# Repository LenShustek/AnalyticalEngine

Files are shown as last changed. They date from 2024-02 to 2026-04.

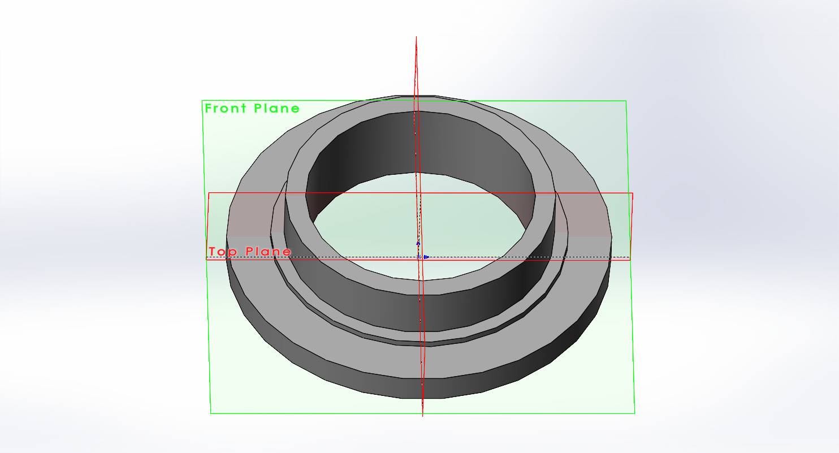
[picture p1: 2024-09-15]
Piers_Plummer_DE/parts/Fig_cyl_end.JPG

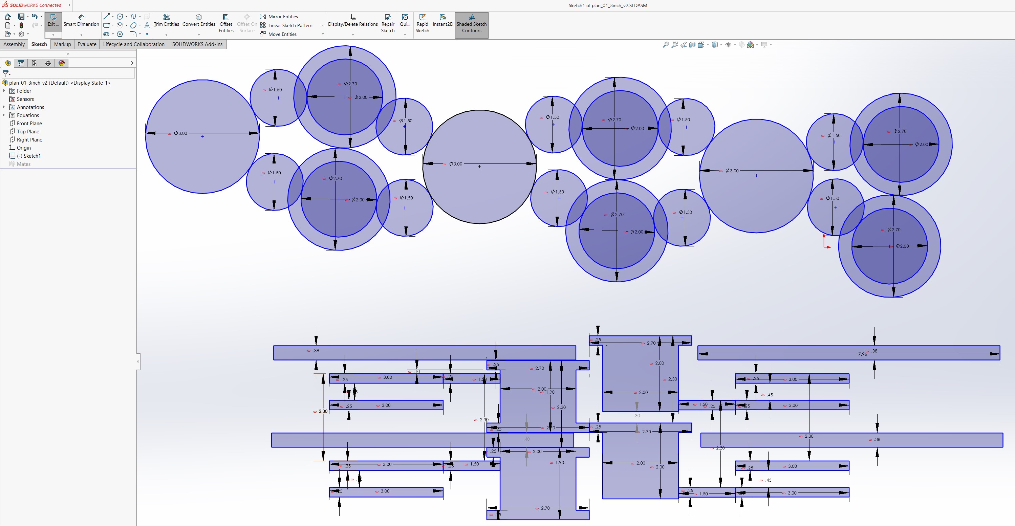
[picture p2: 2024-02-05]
test_designs/mill/plan_01_3inch_v2.jpg

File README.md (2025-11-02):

# Building the World's First Computer

This is a project to build the "first computer": a version of
Charles Babbage's entirely mechanical Analytical Engine. The original proposal is the file <ins>proposal_V0.5.pdf</ins> in this directory.

It is a major undertaking that will take years. As of the start of 2024 the effort has just begun.

This repository will reflect a work continually in progress. It will contain plans, 
notes, simulations, and designs as they are developed. Nothing here is static, and 
no decision is immutable until we start construction, and maybe not even then. 

I posted a 30-minute talk about the project here: https://youtu.be/HRmGAhwOo0s

19 April 2024: As changes are made to reflect progress, this repository is starting to look more like a blog, especially recently in the test_designs/anticipating_carriage section. GitHub is not the right vehicle for that, so I've transitioned instead to using a real blog: https://worldsfirstcomputer.blogspot.com/. I'll keep putting design and code files here, but the narrative (in the conventional reverse chronological order) will now be in the blog.

If you are interested in this project, the place to start is the latest version of the proposal
document in this directory. It will be modified occasionally, but there is a log at
the end that highlights what has changed.

Other directories will appear as various parts of the project are developed. 
These are the first to be added:
- simulations
  - instruction_simulator
  - timing_simulator
  - component_simulator
- test_designs
  - digit_wheel
  - anticipating_carriage
  - mill
     
Wish us luck. 

Len Shustek
4 February 2024

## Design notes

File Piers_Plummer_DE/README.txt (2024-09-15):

An absolutely extraordinary partial model of Charles Babbage's Difference Engine #2 was built in 2017 by Piers Plummer at Royal Holloway, University of London. You can see it in action here:
https://www.youtube.com/watch?v=IhnA-oAwh04
Amazing!

It is a simplified version of the DE with 4 columns of 6 digits each, opened out more than the original design for better visibility. It is made of 3D-printed and painted nylon, laser-cut steel, and other standard modern parts. "And of course, it had to be powered by steam!"

In order to learn from their detailed design, and to see that it gets the public exposure and preservation that it deserves, I asked for and received permission to make the CAD files available in this GitHub repository.

The design files were made with Solidworks. For those of without access to that CAD software, I created and included JPG images of each of the parts and assemblies.

This was a project with the Centre for Software Language Engineering at the Computer Science Department of Royal Holloway, University of London, funded by The Leverhulme Foundation with support from the Engineering and Physical Sciences Research Council. The participants in the project were:
   Dr. Doron Swade
   Prof Adrian Johnstone
   Prof Elizabeth Scott
   Dr. Piers Plummer
http://babbage.csle.cs.rhul.ac.uk

Well done!

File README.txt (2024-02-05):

This is a project to build the "first computer": a fully mechanical version of
Charles Babbage's Analytical Engine. It is a major undertaking that will take years.
As of the start of 2024 the effort has just begun.

This repository will reflect a work continually in progress. It will contain plans, 
notes, simulations, and designs as they are developed. Nothing here is static, and 
no decision is immutable until we start construction, and maybe not even then. 

If you are interested, the place to start is the latest version of the proposal
document in this directory. It will be modified frequently, but there is a log at
the end that highlights changes.

Other directories will appear as various parts of the project are developed. 
These are the first to be added:
  simulations
     instruction_simulator
     timing_simulator
     component_simulator
  test_designs
     digit_wheel
     anticipating_carriage
     mill
     
Wish us luck. 

Len Shustek
4 February 2024

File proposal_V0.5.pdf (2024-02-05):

# Building the World’s First Computer

# Charles Babbage’s “Analytical Engine”

## Len Shustek

4 February 2024, version 0.5

# Introduction

Charles Babbage, as historian Doron Swade likes to say, is equally famous for two things: inventing the digital computer, and failing to build it.

Babbage began his first design for a computer, which he called the Analytical Engine, in 1834, at the age of 43. He worked on that and subsequent designs for most of the next 37 years, until his death in 1871. During that time he created “Plans” for at about 35 different Engines, each with varying degrees of details worked out. Unfortunately none of the Plans was a complete design with a set of drawings from which parts could be built and a computer assembled.

We are left with a rich collection of ideas, drawings, notes, mechanical designs, timing diagrams, and descriptive symbolic “Notations” for an entire family of unfinished computers that no attempt was ever made to build.

The challenge we wish to pose is: Can we, 185 years later, build a fully functional mechanical computer of the kind that Babbage envisioned?

# Contents

# Executive summary

The dawn of the computer age is generally situated in the middle of the 20th century, at about the time of World War II. Although we crave heroic individual inventors for important technological advances – like Bell for the telephone, and Edison for the lightbulb – the situation for the computer is much more complicated.

If, however, we travel back to the middle of the 19th century, we discover a lone genius named Charles Babbage who devoted his life to inventing calculating machines. The most innovative of those machines was a programmable digital computer that he called an Analytical Engine.

The problem with anointing him on that basis as the sole inventor of the computer is that he never built it. We don’t know if his ideas were sound, or if his computer would have worked.

The project we wish to undertake is to build a working version of Babbage’s Analytical Engine, or at least something close enough to it that will demonstrate to the world that he fully deserves to be considered the inventor of the computer.

The Engine we propose to build is an entirely mechanical monstrosity, perhaps 12 feet long, 6 feet wide, and 10 feet high, made of gears, wheels, levers, and cams. It is programmed with “software” that is encoded by punched holes in rigid cards that are sewn together into continuous chains. It is animated by a single rotating shaft, which we would ideally like, in the spirit of Victorian technology, to be powered a steam engine. Useful computations will take 10 to 30 minutes, and the results will be observable afterwards as 30-digit decimal numbers shown on 7-foot tall columns of digit wheels.

This project is likely to take 3 to 5 years and cost 2 to 4 million dollars. The final year is the assembly and debugging phase, which we propose be staged in public view as a “living”
museum exhibit.

Assuming we achieve success and have a reliable operating Analytical Engine, it would then become a permanent, regularly demonstrated, and no doubt wildly popular exhibit.

This is an ambitious project, but the obligation to create a just record of history motivates us to undertake it.

Posterity, and Charles Babbage, deserve it.

# Part 1: the project and its background

# Related Babbage machines

In addition to designing computers, Babbage also designed mechanical calculators he called “Difference Engines”. These were special-purpose non-programmable machines that compute and tabulate values of polynomial equations that can be used to approximate a wide variety of mathematical functions. Like all traditional calculators, they are fundamentally different from computers in that they don’t follow instructions we call “software”. The Analytical Engine, in contrast, would have been of an entirely new and different class.

From 1823 to 1842 Babbage made an attempt to build his first Difference Engine using funding provided by the only venture capitalist of the day: His Majesty’s government. The project ended as a complete failure for a variety of reasons, including that Babbage had become more interested in his new idea for a computer.

Between 1846 and 1849 Babbage took time off from working on the computer to design an improved calculator, Difference Engine #2. He completed the design in full and meticulous detail, but he made no attempt to build it.

Some 140 years later, from 1985 to 1991, Doron Swade at the Science Museum in London led a bold project to build Difference Engine #2 exactly according to Babbage’s plans, with fabricated parts that have mechanical tolerances no better than what Babbage’s machinists could have achieved. It was a spectacular success. The machine works perfectly, demonstrating both that the design was correct and that Babbage could have built it. We can only conclude that the reasons for his failure were managerial and organizational, not technical.

Is the same true of his computer, the Analytical Engine? With the right management and funding, might we have had a computer a century earlier than we actually did?

The Science Museum ultimately built two copies of Difference Engine #2 as well as the integrated printer that was also designed by Babbage. The first copy stayed there and is run by curators only occasionally. The second one was loaned by its private owner to the Computer History Museum in California, where it was demonstrated by volunteer docents daily for 8 years, to the amazement of hundreds of thousands of visitors. In 2016 it was moved to the owner’s personal site and is now also rarely operated.

# On the prospects for building a complete Babbage Analytical Engine

There is a long-term vision for a project that would choose one of Babbage’s 35 plans for Analytical Engines, complete the many parts of that design that he had left undone, and build it as an historically accurate incarnation of one of his imagined computers.

This may someday be possible. But building an engine that adheres strictly to any of Babbage’s Plans is a massive undertaking and will be very difficult. Here are some of the issues:

- Only the later engines, starting with Plan 27, have conditional branches and loops that qualify them as modern-style general-purpose computers. Earlier designs do not, and so are less interesting as precursors of what was reinvented in the 20th century.
- Babbage prized both generality and high performance, with the result that all of those later Plans are frighteningly complex.
- The design for the chosen Plan would have to be completed in a way we might imagine him doing. There are substantial subsystems (like the interaction between user-level instructions and the microcode, and the transmission of barrel¹
stud movements to the
rest of the machine) as well as many important smaller mechanisms that are not designed. It is not just a few minor details that are missing.
- The complex mechanisms he did design have never been built or simulated, and some of them (like the selection mechanism for table-driven division) are devilishly hard to understand. We would have to convince ourselves, by reasoning or by simulation, that they would work correctly.
- For historical authenticity there might be pressure to use only materials and perhaps even methods that would have been available to Babbage, which increases the difficulty. It will be a challenge. In 2012 Doron Swade said of the magnitude of such a project²
, “I
reckon on 15 to 20 years to construct, and between 20 and 40 million dollars”.

1 The “barrels” are rotating cylinders with vertical columns of preset studs that control operations in the machine during a cycle, which is either 15 or 20 basic time units. The barrel rotates to a new position for each cycle by an amount that may depend on the data being manipulated. Depending on the Plan, Babbage proposed from one to five barrels, each of which can be viewed in modern terms as an independently executing microprogram.

2
“Mission Impossible: Constructing Charles Babbage’s Analytical Engine”, Dartmouth University, 8 May 2012, https://www.youtube.com/watch?v=FFUuN-ZRLz8

# The proposed project

As an alternative -- or perhaps as a prelude -- to choosing, completing, and constructing an historically accurate instantiation of one of the full Babbage engines in the course of a 15 to 20 year project, I propose that we build a “Babbage-inspired” smaller Analytical Engine. It will still be a fully-functional mechanical digital computer run by software, but it will be much simpler because it implements only a subset of the many features that are in Babbage’s highly developed Plans.

In 1840 Babbage briefly considered such a machine, designated as Plan 26, but he was discouraged by the poor theoretical performance and did not pursue it. Again at the end of his life he considered -- and actually started constructing -- a different simplified engine that he called “the Model”, which might be considered his final Plan 35. The incomplete fragment he built is at the Science Museum in London, but no drawings of what he intended for the complete machine survive.

The functionality of our proposed small engine is in line with both of those. Our goals are threefold:

- to gain experience with constructing a mechanical computer using Babbage-designed mechanisms that might inform later attempts to build one of the complete Babbage engines
- to help justify the assertion that Babbage is the inventor of the computer
- to create an engaging public museum exhibition of a programmable computer that could have been built a century before it was actually first achieved

We are not overly concerned with performance, because we can choose specific demonstration problems that execute in a reasonable time given the characteristics and generality of the smaller engine. We wish instead to emphasize the novel and prescient aspects of his instruction sequencing and microprogram control, which predated the reinvention of electronic equivalents by over a hundred years.

Will this be an “authentic” Babbage Analytical Engine? No, and yes.

No, in that we are not implementing a specific Babbage design, and we are not using only materials that he would have used. It will not look in its details exactly like an engine he could have built, and it will not have some internal features that were in many of his designs.

Yes, in the sense that it is it is an honest amalgam from several of his designs. It will use only architectures and mechanisms he designed, and it will functionally be a faithful subset of many of his unbuilt computers. It fully inherits the spirit of his ambitions.

We will be careful to describe this not as “The Babbage Analytical Engine” (as if there were one), but as a “Babbage-inspired”, “Babbage-like”, or “Babbage subset” computer. See Appendix 1: proposed exhibit placard.

# Related projects

There is a complementary formal organization already in place. Plan28 (www.plan28.org) was established in December 2011 as UK non-profit charity #1145043 whose stated mission is “to build a Babbage Analytical Engine for historical and educational purposes.” It has four volunteer trustees (Doron Swade, John Graham-Cumming, Tim Robinson, Johnathan Rosser Histed) and no employees. The reported total gross income has been less than £1K per year since inception. Its 2013 appeal to accumulate financial pledges on www.justgiving.com has been suspended. As of March 2023 several attempts to solicit additional participation in the activities of Plan28 had not been successful

After 12 years, the major accomplishment of Plan28 has been the incredible six years of work that Tim Robinson (a docent at the Computer History Museum in California) has done as a volunteer, cataloging and analyzing the 7000 pages of documents that Babbage left behind relating to the Analytical Engine. Tim is writing what will be the definitive scholarly exposition on the evolution of plans for the Analytical Engine during Babbage’s lifetime.

Tim’s work is monumental, and provides important background for understanding Babbage’s designs. But it does not contain within it a proposal for a modern construction project. No resources have been applied to that.

The Plan28 project is committed to choosing, completing, and faithfully building one of Babbage’s full designs, and doing it in the UK. Our goal is to build a reduced design, and to do it in the US. The projects are compatible and harmonious, but different and independent.

# Project phasing, timeline, cost, venue, and funding

Doron Swade’s estimate of 15-20 years and $20-40M for the full engine build was based, as he says, “on the classic and traditional engineering fudge factors, guess work, divination, [and] astrological prediction”.

At this point we can do no better than that for the proposed smaller engine. We have only uninformed wild guesses, of which this is the first one:

phase | for what | time | money
1 | architectural design, including register-level simulation | 6 months | $0
2 | detailed mechanism design, including some mechanical connectivity simulation and prototype construction; develop test and evaluation plans | 1 year | $0
3 | CAD part drawings, including limited motion simulation of some subsets | 1 year | $250K
4 | part fabrication and procurement | 6 months | $1M
5 | assembly and debugging | 1 year | $250K
| totals | 4 years | $1.5M

The cost for parts was guesstimated thusly: The most numerous part is the digit wheel. We have a quote of less than $2 each for 3D-printing them in China out of nylon. We need about 1700, so $3400. Quadruple that cost to account for metal shafts and surrounding supports, so $14K. Assume we need 4 times as many parts for the rest of the engine (so 6800, of which some are custom and some are stock) that cost $150 each on average, and the total comes to $1.03M³
This is, of course, a gross and premature estimate.

The two chunks of $250K are for professional salaries. The rest of the labor, including management, comes from volunteers. We might be able to get some contributed professional labor from related companies, like Autodesk.

Clearly these completely fabricated estimates cry out to be quickly and periodically refined as the design becomes more specific.

3 Note that the most numerous part – the figure wheels – are an insignificant part of the total!

The first four phases require no venue, other than modest storage for parts as they arrive during phase 4. Assembly would most preferably happen as a year-long public exhibit at the Computer History Museum in California, at no cost for the space. The machine would then, if successful, become a permanent museum exhibit and be operated daily by trained volunteer docents.

I expect that raising $1M to $2M ($2M to $4M if we are off by a factor of 2) for this project from a small number of interested individual donors will not be difficult. Corporate sponsorships are also possible and would be welcome.

This is a difficult but definitely achievable undertaking that will be a major contribution to the history of computing and therefore of our modern age.

# Part 2: technical details

We here codify two sets of propositions for the construction of the small engine:

1. guiding principles for making design decisions, including those that will allow the engine to qualify as “Babbage-inspired”, or “an amalgam of Babbage’s designs”
2. the design decisions, based on those principles, that determine the detailed characteristics of the Engine we will build
These are strawman proposals. After they have been debated, modified, and accepted, we can move on to the next phases of the project: detailed design, simulation at several levels, part drawings and specifications, prototype testing, fabrication, and assembly.

# The principles

1. The top-level goal is to exhibit the practicality of a general-purpose programmable mechanical digital computer that could have been built using Babbage-designed mechanisms in the 19th century. It is not, as was motivating Babbage, to build a machine that will actually be used for utilitarian table-making, or for novel mathematical research.
2. We are not picking one of Babbage’s extremely complex Plans to implement. None of them were complete, and some of the Plans closest to being complete violate other of these principles.
3. We are instead building an Engine that is “inspired by” Babbage’s designs. We will pick from among his algorithms and mechanisms, from whichever of his Plans they were in, to create an achievable modern Plan that has a high likelihood of success.
4. We will include all the features necessary to demonstrate that the engine is a fully general programmable computer in the spirit of those we build today. That includes the ability to create program loops, and to execute conditional transfers that are based on computed results.
5. Maximum performance is not an objective, as it was for most of Babbage’s Plans. Our objective is “reasonable” performance that is suitable for demonstrations.
6. We place high value on simplification, subject to the “reasonable” performance objective.
7. We place high value on avoiding the use of untested or novel mechanisms that might increase the risk of failure.

8. We place high value on having only one kind of each distinct part type, not multiple variants. So, if we can: only one kind of Figure Wheel, only one kind of barrel pickoff lever, etc.
9. All things being equal, we would prefer to make more copies of a smaller number of parts that we can develop high confidence in, rather than to use unique, unproven, or complex mechanisms.
10. We will primarily use architecture and mechanisms that had been proposed by Babbage for some Plan, or variations of them that we could easily imagine him devising given the appropriate motivation. We are rarely if ever allowed to invent new mechanisms, and only if the need is compelling, and only if they are in the style of those he devised.
11. We will not be constrained to use only engineering processes that were available to Babbage. We unapologetically use modern tools for simulation, design, and manufacturing.
12. We will not be constrained to use only materials that were available to Babbage. Plastic parts fabricated using 3D printing, for example, are fair game.
13. We wish the resulting Engine to be demonstrated regularly in a museum environment, so we will need to choose and achieve appropriate quantitative targets for performance, life expectancy and reliability.
14. Our focus is on building the calculating engine. We will leave the building of printing⁴ and/or plotting apparatuses, both of which interested Babbage, to future generations.

4 Note that the printer designed by Babbage for Difference Engine #2 and built by the Science Museum London in the 1990s would work equally well, with minor changes in the interface, for the Analytical Engine.

# The design decisions and the rationales therefor

1. Numbers have 30 digits.
- Babbage’s designs varied from 25 to 60 digits per number, stored as a set of rotating “digit wheels” that are stacked vertically on a common axis with the units position at the bottom. That may at first seem like an excessive number of digits, but because there was no floating point number representation, long numbers are required to support a large dynamic range.
- 30 digits is more than adequate for demonstration purposes. We could even do with fewer.
- Increasing the number of digits in numbers has a surprisingly modest impact on the details of the design. But it does increase drive force requirements, change the framing system, increase the overall height, and increase cost. We would do that only if further analysis provides the justification.
- The Difference Engine #2 built in the 1990s had 31 digit numbers, so we would be in good company. We would feel comfortable about the complexity and utility anywhere in the 20-40 digit range.

## 2. Use sign-magnitude representation for numbers in the

store.

- Babbage proposed this representation in all mature versions of the Engine.
- The sign is stored on an additional (31st) Figure Wheel, with any even number representing positive, and any odd number representing negative.
- This is convenient for user interaction, and for multiplication and division.
- It does complicate addition and subtraction, which will sometimes require extra cycles to convert to 9’s complement form suitable input for the adder, and to convert negative numbers back to sign-magnitude for storage.

## 3. Use 9-cycle whole-zero operations for Giving Off⁵ transfers

- Starting with Plan 28, Babbage proposed a clever “half-zero” idea which almost doubles the speed of transfers by turning wheels in either direction during Giving

5
“Giving Off” is the process of rotating all the digit wheels of a number axis so that they become zero, while at the same time adding the original values to the digit wheels of another axis. When using “whole-zero“ it takes one cycle of 15 time units: 1 time unit for receiving the directive from the microprogram barrel, 2 for putting the axes into gear, 9 for the rotation, and three for engaging the locks that prevent any further movement of the wheels.

Off. But it almost doubles the number of wheels, and it adds complexity to the Anticipating Carriage. We do not embrace that tradeoff.

## 4. Do addition using an anticipating carriage

- Babbage was justifiably proud of his clever design that performs all the carries for a multi-digit addition in parallel, in a small amount of time that is independent of the number of digits in the values being added.
- We accept the complexity of this mechanism both to improve performance for a common operation and to honor the genius of its inventor.
- We do not implement his “hoarding carriage” for consecutive additions that accumulates up to 10 carries for later inclusion into the sum.

## 5. Multiplication and division are implemented without using a table of multiples of the multiplicand or divisor

- Most of Babbage’s mature Plans precomputed nine multiples of the multiplicand or the divisor, in the interest of increased speed during the computation of the product or quotient.
- That scheme requires nine additional “Table Axes” to be built, and several cycles of additional overhead time at the start of a multiplication or division. It represents a significant increase in parts and complexity.
- In many cases it also results in a significant performance improvement. But it actually reduces performance for some simple cases where the overhead of constructing the tables dominates.
- To support our decision not to use tables, I did timing simulations using random operands of various lengths. See Appendix 2: multiplication and division timing charts for graphs that elucidate and quantify the cases where the tables help. The conclusion is that we can minimize the performance hit of not using tables if we avoid long multipliers and long dividends with small divisors.
- We will select demonstration programs so that the lack of precomputed tables is not a serious issue. Babbage, in his quest for general applicability of the engine to a wide range of problems, did not have that option.
- That said, it is historically important that we be able run the program to compute Bernoulli Numbers whose trace Ada Lovelace documented in Note G of her 1843 translation of Luigi Menabrea’s paper on the Analytic Engine, and in that case we will suffer from not using the tables. See Appendix 3: calculating Bernoulli numbers.

- Babbage eliminated the tables twice: once for the short-lived Plan 26 in 1840, and again for what Tim Robinson calls Plan 35 in 1869-1870. Babbage called that his “model”, and used the design to actually start construction, for the first time, of an Analytical Engine. It was still incomplete at the time of his death in 1871, but the fragment is preserved in the collection of the Science Museum in London:
https://collection.sciencemuseumgroup.org.uk/objects/co62245/babbages-analytical-engine-1834-1871-trial-model-analytical-engine-mill (https://collection.sciencemuseumgroup.org.uk/objects/co62245/babbages-analytical-engine-1834-1871-trial-model-analytical-engine-mill)

## 6. Multiplication will generate only a single-precision 30 digit result

- Many of Babbage’s Plans generate a double-precision result from multiplication that is stored on two axes, so that (1) all product digits are always retained, (2) overflow cannot happen, and (3) the result can be used as a double-precision dividend for division by a single-precision divisor.
- But doing so requires complexity which we think is not worthwhile for our smaller engine.
- We will instead detect overflow during single-precision multiplication and signal it to the operator, which is a scheme that Babbage proposed to use in several other cases.
- This is not an uncommon limitation for later computers. Having a single-precision multiplication result matches the model of integer arithmetic implemented a century later by most programming languages. When you multiply two integers in Fortran or C, you don't get a double-precision result that can then be used as the double-precision dividend for a division. It is true that in that environment there is the option of switching to floating point for greater range. But their integers don't hold the equivalent of 30 decimal digits, so the need for floating point is more pressing. And anyway the early floating point formats, like for the IBM 704, had a maximum single-precision exponent of only 2

128 (10³⁸)so they
were not that much better than 30-digit integers. We would be quite happy if our Analytical Engine had computational capability similar to the IBM 704 from 1954.

## 7. Implied decimal points are implemented

- In some Plans Babbage allowed the user to specify an implied decimal point that was “d” digits to the left of the least significant digit.
- The source of “d” isn’t always clear. In Plan 13 it is assumed to have been set manually by the operator on a special figure wheel of a particular Mill axis.

- Implementing this requires additional barrel microcode complexity, and additional time for division to generate more quotient digits. For multiplication, the required right shift of the product might overlap with other operations and take no extra time. There is no impact on addition and subtraction.
- We initially decided against implementing this. But the desire to execute, unmodified, the famous 1843 Lovelace program to compute Bernoulli Number B7 caused a reversal of the decision.
- The alternative is to require the programmer to scale up operands appropriately, and to use the explicit shift (“step up” and “step down”) instructions when necessary.

## 8. Square root is not implemented

- This was a feature in early Plans, but by Plan 16 even Babbage had discarded it, complaining that “It doesn’t do cube roots.”

## 9. Approximate multiplication and division is not implemented

- In some Plans Babbage proposed versions of multiplication and division that were faster because they operated on fewer digits. He thought they would be useful for certain mathematical approximation methods, which typically do not require full precision in the early stages.
- If this requires more than a trivial modification to the full-precision algorithms, it is not worth the additional complexity. But if it is simple, and if it speeds up no-table multiplication and division, it may be worth doing.

## 10. We do support pipelined streamed addition/subtraction

- In some Plans Babbage allowed for a succession of variables coming from the store to be added to an accumulating value in the mill. All, some, or only the final value of the sum is written back to the store, as directed by the cards.
- Babbage didn’t, unfortunately, provide modern-style registers -- or even a single accumulator – to retain data in the mill between operations. Hence computing the sum of a sequence of values without streamed additions is painfully slow, since each intermediate value has to be written back to the store and then reread. A simple addition or subtraction of numbers in the store takes 6 cycles of 20 time units each, or about 19 seconds. Adding ten numbers would take 190 seconds.

- With pipelined streaming, adding ten variables takes about 44 seconds instead, a 4.3x improvement. That is a significant enough savings for a common operation to warrant the extra complexity.
- This is also a stellar demonstration of “microcode” in Babbage’s design that is distributed among independently operating barrels.

## 11. The store

- The store will contain 25 axes. Each axis has 31 cages

6
, and each cage holds two
digits, for a total storage of 50 signed 30-digit numbers in sign-magnitude format.
- ENIAC, which after its 1947 conversion was the first stored-program electronic computer to solve serious research problems⁷
, had only 20
10-digit numbers. We will have over twice that in both metrics.
- The store is arranged linearly, with transfers to the Mill effected via straight geared racks.
- Readout from the Store is not destructive, because returning the racks to their home position after “giving off” and transferring the value to the Mill will restore it to the Store axis. (There is a suspected timing problem in Babbage’s design for this that will need to be resolved.)

## 12. On the engagement of axes

- We will investigate having axes engage with racks and with other axes by being raised or lowered, which also selects one of the two numbers. There is then no need for additional axes with pinion gears.
- This was proposed by Babbage in Plan 28, although we are not also adopting that Plan’s half-zero scheme for giving off.
- The feasibility of doing this will depend on the geometry of the machine layout in the various areas. In the Mill, additional columns with small pinion gears may be necessary to engage figure wheel axes that can't be put close enough to another to allow lifting to effect engagement with their intended partner.
- Raising and lowering axes to effect engagement may also complicate the support structure that keeps digits wheels separated by a constant distance.

6 A “cage” contains two or more adjacent digit wheels from unrelated numbers at the same decimal position on an axis. See Digit wheel parameters.

7
See the description of Klara von Neumann’s Monte Carlo simulation program for hydrogen fusion as described in “ENIAC in Action” by Haigh, Priestley, and Rope, MIT Press 2018.

## 13. The user-level instruction set

As Tim Robinson says in his treatise, “This is perhaps the least well elaborated aspect of the mature Engine, and one in which he [Babbage] showed much indecision.”

We will need to define the format and encoding for Operation, Variable, and Number cards, which together form what is today called a program. Each type of card is fed as a separate connected loop to one of three card-reading prisms.

Focusing on the Operation cards, we propose the following for what we would today call the “machine language instruction set”:

1. algebraic addition
2. algebraic subtraction
3. algebraic multiplication, producing a 30-digit result
4. algebraic division, using a 30-digit dividend and divisor
5. ascertaining if a variable is zero
6. ascertaining if a variable has a positive or negative sign
7. reading a number card into storage
8. stepping up (multiplying by 10)
9. stepping down (dividing by 10)
10. turn cards forward (forward jump; see S/2/2.339 in the Babbage archive)
11. turn cards back (backward jump; see S/2/2.339)

Except for the change to single-precision for multiplication and division, these are all operations that were proposed by Babbage for Plan 27.

Pipelined streamed addition or subtraction doesn’t require an additional instruction type because it is encoded on the normal addition or subtraction operation card. We can choose one of the two possible schemes Babbage described:

1. The operation card (or a Store location) contains an index which indicates the number of operands to be operated on, each fetched using a new variable card. When all the operands have been processed, a second addition or subtraction operation card then orders the result to be written to the store. The semantics of addition and subtraction instructions are thus context sensitive.
2. A new operation card is read with each variable card, and it indicates when the accumulated result should be written to the store. In this case multiple partial results could be written.

The critical new features in Plan 27 were the tests (5 and 6), which make the Analytical Engine a universal Turing-complete computer. The design, however (quoting Tim Robinson), “is not very clear regarding the actions that will be taken depending on the result of the test.” It is most likely that small indices on the operation and variable cards indicate how many of those types of cards should be skipped, and whether in the forward or backward direction, if the condition being tested is satisfied.

## 14. Digit wheel parameters

The digit wheel is the basic storage unit for one decimal digit. Its geometry affects everything in the engine.

- considerations for the digit wheel size:
- In all of Babbage’s designs through Plan 25 the diameter of the digit wheels were 4”, although some isolated wheels on certain axes in the Mill were as large as 8”.
- In Plans 27 and 28 he changed to 3” wheels for the store and table axes.
- In plan 30 he reduced it further, to 1-1/4”.
- Smaller wheels are better because the mass (proportional to the square of the diameter) is reduced, and because it allows axes to be placed closer together, which in turn reduces the required size and mass of racks and the supporting framework.
- But smaller wheels are worse because they require more precision, and even small accidental motions can cause derangement.
- considerations for interleaving the digits of multiple numbers on one axis:
- All number columns in the Mill and the Store must have the same inter-digit spacing.
- The inter-digit height required by the anticipating carriage mechanism leaves room for 2 or more digit wheels from separate numbers to be stored at each of the 30 digit positions along an axis.
- Plans 1 to 13 used 3-5/8” high cages that hold digits from 4 different numbers.
- Plans 14 to 27, thanks to a more compact mechanism Babbage devised for the anticipating carriage, used 2-7/8” high cages holding digits from 2 different numbers.
- Plans 28 used 1-5/8” cages with 2 numbers.
- Plans 30 and beyond proposed using pressure die casting or metal stamping to achieve cage heights of 5/8” or even smaller.

- We propose to adopt the Plan 27 intermediate wheel size and its corresponding cage height, digit spacing, and digit speed. The complete set of wheel parameters is thus:
- DP (“diametral pitch”) of 10, which means 10 teeth per inch of diameter
- That sets the size of the teeth and the width of locking bars
- 3 inch diameter wheels, so 30 teeth/wheel
- 3 copies of 0..9 on each wheel, which means a 0.314 inch “unit of space” between digit positions, and one tooth per digit position
- 2 inch/second maximum surface speed, which means a 0.157 second “unit of time” for single digit position movements
- preliminary investigation indicates that the cage height could be as small as 2.3 inches
- 2 digits per cage
- a 30-digit column plus sign that holds two numbers is then about 6 feet high
- There is mechanical overhead, mostly underneath the digit columns, that will occupy an additional 3 or so feet.
- For maintenance it may be necessary to allow enough ceiling height to pull an axis out the machine vertically. That could require about 16 feet of ceiling clearance above the floor.
- The same digit wheel configuration is also used in the Store, which therefore holds twice as many numbers as it has axes.
- In the Mill, some of the axes may only need or require only 1 digit per cage.
- In general we will endeavor to use this as the only figure wheel format in the engine, consistent with principle #8.

## 15. Powering the engine

In the interest of making the museum experience as historically authentic as possible, it would be gratifying to be able to power the machine with a live steam engine.

The steam engine would need to be of the condensing kind -- not to improve efficiency, but so that steam is not vented indoors. The boiler would be modern, electric⁸
, and located outside the demonstration area.

8
Like, for example, https://catalog.electrosteam.com/item/process-steam-generators/lg-10-40-electric-steam-generators/lg-10-h (https://catalog.electrosteam.com/item/process-steam-generators/lg-10-40-electric-steam-generators/lg-10-h)

It is not clear if we can pull this off. Steam-operated equipment is generally subject to extensive safety, inspection, and even training/certification regulations. Since our boiler would be less than 400,000 BTU/hour it would be exempt from many of the regulations, but it would still likely require a waiver of normal building codes to secure a permit for installation.

Providing power in the 2-5 HP range should be easy, but at this point we don’t know what will be required.

Using compressed air to drive an air motor could be an appropriate and less problematic substitute for a steam engine. Practical electric motors were invented around 1840 and were not in general use until the 1880s, so using one of those, if we had to, would be an anachronism.

## 16. Units of measure

- Although most modern mechanical designs are done in metric, we will use U.K. imperial units in deference to the 19th century convention of Babbage’s time. It is, thankfully, still common enough as to not cause raised eyebrows from our suppliers or fabricators.
- Drawings will be dimensioned in inches and decimal fractions of an inch.
- Unlike Babbage, we get to take advantage of standardized parts:
- For screws and bolts we will use imperial diameter gauge (4, 6, 10, 12, 1/4”, 5/16”, 3/8”, 7/16”, 1/2”) with pitch in standard threads per inch (40, 32, 24, 20, 18, 16, 13).
- We will use the now ubiquitous 1918 standard UNC/UNF (Unified National Coarse/Fine) 60o

thread profile, not the 1841 Whitworth 55o profile that Babbage would have used.
- For stock metal we will buy inch-denominated parts, as in
0.125" x 1" x 72” 1144 alloy steel rectangle bar.
- We will try to use only standard 20° pressure angle involute spur gears, chamfered on the face edge when necessary for axial mating.

## 17. Design decisions yet to be made:

- the plan view specifying the arrangements of axes, racks, microcode barrels, etc.
- the microcode barrel structure: how many, the distribution of functions, and the assignment of studs to operations
- the detailed microcode barrel programs

- the linkages for transmitting the bits in the current microcode word to the parts of the machine controlled by it
- an outline of the support structure
- the choice of material for each part
- the details of providing power
- encodings for operation, variable, and number cards
- any I/O we want aside from the programming cards as input and the bell as output
- provisions for modern high-tech auxiliary equipment, like cameras for reading out the values currently in the Store or in the Mill
- features that should be added specifically for debugging and status monitoring
- more?

# The CAD system

For 3D printing experiments I first used Autodesk Fusion/360, which is the modern alternative to the venerable and groundbreaking 40-year-old AutoCAD.

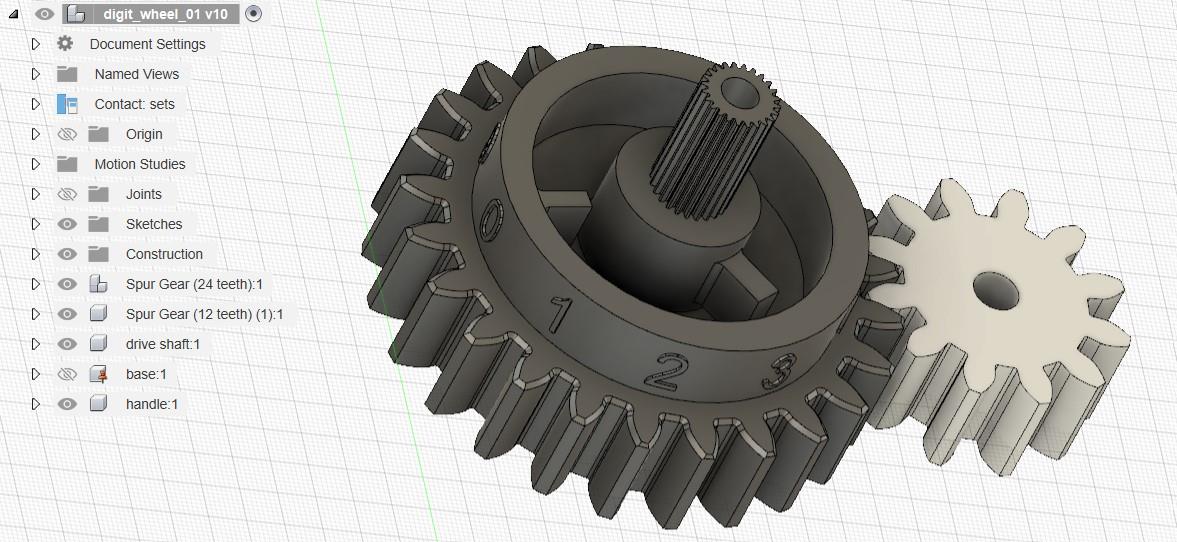
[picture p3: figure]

I then fabricated prototype designs out of PLA polyester with a LulzBot TAZ 6 desktop 3D printer, https://lulzbot.com/store/taz-6. The results are surprisingly good, even with no after-print finishing.

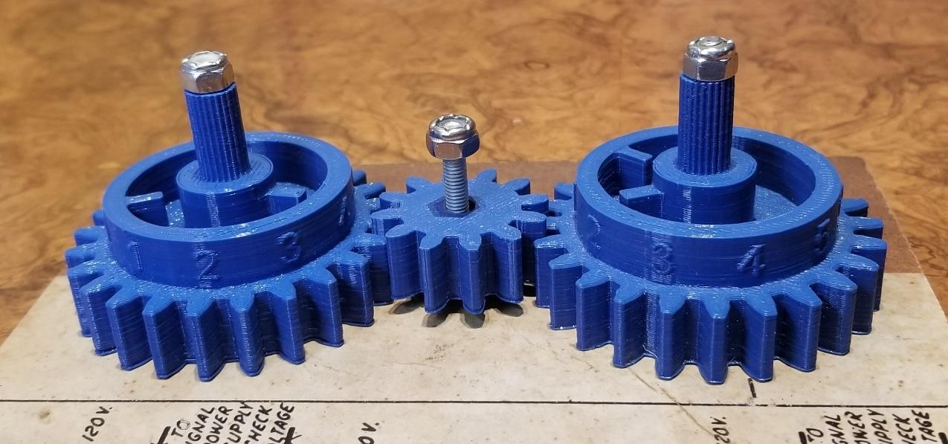
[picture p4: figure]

If we decide on using 3D-printed plastic parts like these for the finished engine we would switch to a more durable plastic, like Nylon or one of the new Igus abrasion-resistant composites⁹
, and
choose appropriate surface finishing techniques. We may also want to use a two-nozzle head

9 https://www.igus.com/3d-print-material/3d-print-filament that would allow us to print some features, like the raised lettering on the digit wheels, in a contrasting color.

I have since switched to experimenting with SolidWorks Connected from Dassault Systèmes, because it is generally considered a more professional CAD system and has better simulation facilities. Currently under development is a proposed digit stack configuration, a version of Babbage’s clever anticipating carriage, and parts of the Mill.

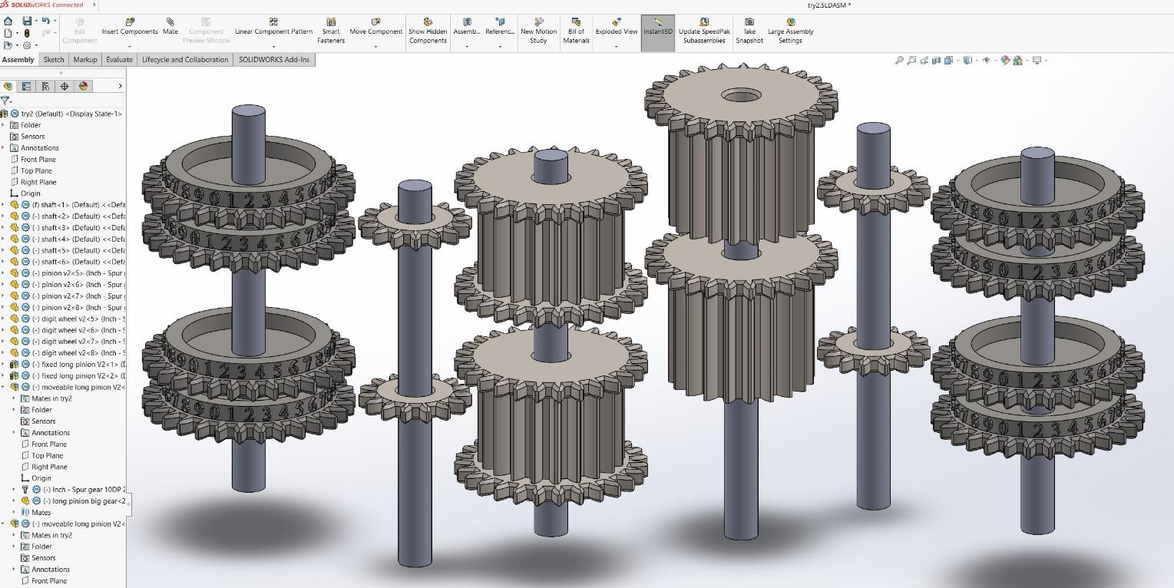
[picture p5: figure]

# Simulation opportunities

In evaluating the machine that is implied by these design decisions, we are privileged to have a tool Babbage didn’t: a computer that can simulate a computer that has yet to be built. We can take advantage of that at many levels:

1. An instruction simulator of the programmer-accessible instruction set and the machine operation focuses on the preparation of operation/number/variable cards and the resulting output. The details of instruction execution are not modeled, although rough timing may be. It is useful for experimenting with and debugging programs.

This was the level of John Walker's web-based JavaScript "Analytical Engine Emulator" that he wrote over six years ago: https://www.fourmilab.ch/babbage/contents.html. It is not currently an active project, and it doesn’t use the exact instruction set we will implement.

I have recently implemented an assembler, disassembler, and simulator in Python for The user-level instruction set we are proposing. It generates the Operation, Variable, and Number card stacks that the engine would use. Test programs written and simulated so far are for the computation of Bernoulli B7, B5, and B3, Fibonacci Numbers, and the Greatest Common Divisor using Euclid’s algorithm. See Appendix 3: calculating Bernoulli numbers and Appendix 4: additional simulated example programs.

2. A timing simulator understands the algorithms used for internal operations with just enough detail to compute how long things take. It does not model the mechanical components. It can be used to predict the performance of the machine and help in choosing between alternative schemes.

I have written a timing simulator like that in Python for the basic operations and used it for the analyses in Appendix 2: multiplication and division timing charts and Appendix 3: calculating Bernoulli numbers.

3. A component simulator models the various functional components and internal operations of the mill and store. This is similar to the Register Transfer Level (RTL) architectural description of modern electronic computers.

Components include number wheels with and without a carriage mechanism, axes with one or more sets of wheels, axes with only interconnecting pinions, microcode barrels, racks, card reading stations, etc. Operations include engagement of axes to other components, giving off a column of numbers with or without stepping, advancing a barrel, propagating carry prediction, etc. It models only function, not the geometry of individual mechanical parts or how they are interconnected. It is useful for understanding and validating the algorithms and their detailed internal sequencing.

I have written such a simulator in Python that so far implements about one third of a complete Analytical Engine. It includes an assembler and disassembler for the microcode programs that are coded into the position of studs on the barrels. The simulator operates at the resolution of the 0.157 second “basic unit” of time, and attempts to mimic the inherent parallelism that the mechanical computer will have. The only test so far has been of a barrel microprogram that implements unsigned multiplication. See Appendix 5: component-level simulator.

4. A mechanical connectivity simulator models the movable mechanical components and how they interact with each other to create chains of motion. It does not model the physical shape or location of components, although it does keep track of their position within a range of possible articulation. It can detect movement which is insufficient or excessive to achieve a desired outcome, but it does not in general detect interference between parts. It is useful for debugging the mechanical details of the algorithm implementations.

Tim Robinson has written a simulator like this in Ruby, which he successfully used to model details of Babbage’s Difference Engine #2. He is now applying it to some of the mechanisms in the Analytical Engine.

5. A detailed machine simulator uses the dimensioned part drawings in a CAD system to model the motion of the actual parts we want to build. It would verify both correct operation and the lack of interference. This is useful to give us confidence that the built parts will work when assembled.

I have hinted at this direction using a "Motion Study" for an Autodesk Fusion/360 model that shows a figure wheel giving off its value. Here is a link to the video:

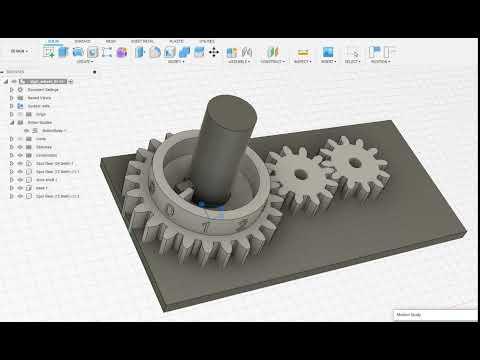
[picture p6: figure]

Figure 1: click to play

We don't yet know if Fusion/360 or even SolidWorks is an appropriate tool for simulating the larger assemblies. But regardless of the CAD system, the whole of the AE can probably not be modeled and we will need to choose only specific subsystems to simulate.

6. A dynamics of motion simulator adds to the detailed machine simulator a model of the forces and stresses on components. This is a feature of many of the advanced CAD systems, often using finite element analysis techniques.

# Appendices

# Appendix 1: proposed exhibit placard

Aside: “185 years” is the time from Plan 27 (1842) to 2027. That gives us 4 years to build it!

# What is this machine?

Charles Babbage – a mathematician, philosopher, inventor, and mechanical engineer – created 35 incomplete designs for mechanical digital computers he called “Analytical Engines”, from 1834 until his death in London in 1871. He made no attempt to build, or even to complete the plans for, any of them.

This fully working mechanical computer is a simplified amalgam of mechanisms taken from several of Babbage’s historical designs. It is not “one of Babbage’s Analytical Engines”, but rather “a Babbage-inspired Analytical Engine”.

We included the following features that were in many of Babbage’s designs:
- a central processor (the “Mill”) that is separate from memory (the “Store”)
- user-level program control using software stored on operation and variable cards
- program loops and conditional transfers based on computed values
- internal control using multiple parallel microprograms
- geared decimal digit wheels stacked to create 30-digit numbers
- addition and subtraction using an “anticipating carriage” for carries and borrows
- multiplication and division as primitive hardware operations
- a settable implied decimal point
- pipelined accumulation of sums
We omitted the following advanced features that are in many of Babbage’s designs:
- table-based multiplication and division
- double-precision and reduced-precision results
- multiple-position shifts
Although Babbage never built any of his calculating engines, his incomplete designs provide clear evidence that he was a genius.
This operating computer, built 185 years later, provides proof.

# Appendix 2: multiplication and division timing charts

A simulation in Python was done to understand the advantage of precomputing the nine multiples of the multiplicand or the divisor. The charts below show the average, minimum, and maximum of the total time¹⁰ and the cycles per digit when multiplying or dividing by a random number whose length is first randomly chosen from 1 to 30.

For extremely short multiplicands and dividends, generating the table makes the operation take longer than the simple no-table algorithm. The initial overhead is just not worth it.

For moderately sized multiplicands and dividends, the average times are not much different. But for a few values, the non-table version is quite a bit slower.

Only for large multiplicands and dividends is the table-based version almost always significantly better.

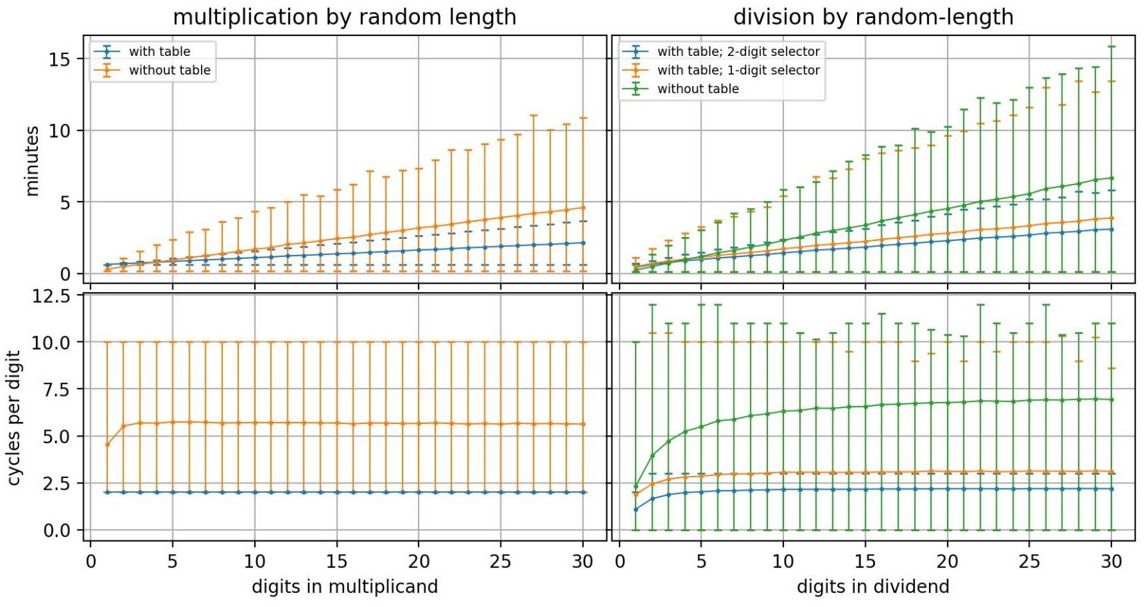
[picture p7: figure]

10 The timing simulator uses several approximations that still need to be verified or made more precise, including a fixed 20-unit cycle time, and other assumptions about how many cycles certain setup and overhead operations take.

For another visualization of multiplication and division timing, I computed the average time to multiply or divide 1000 random numbers for various combinations of operand lengths. The conclusions are the same: for short multipliers, and for divisors that are long relative to the dividend length, the pre-computed tables generally don’t confer a huge advantage and sometimes makes it slower.

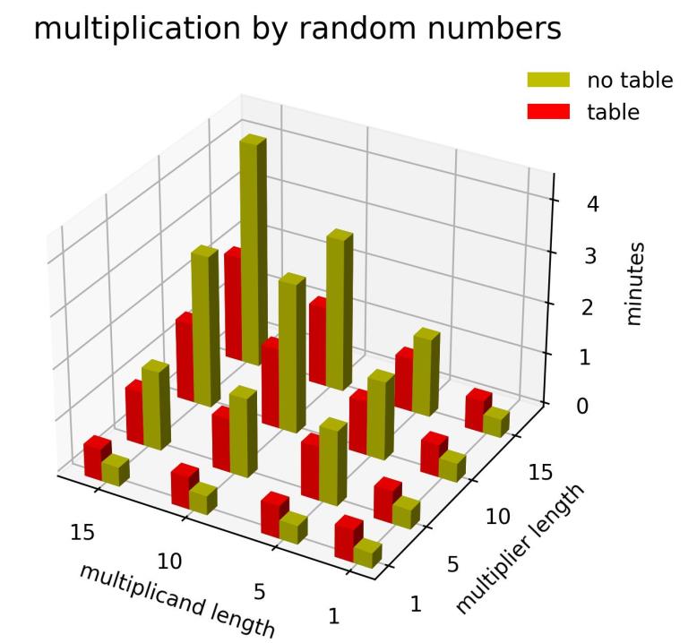
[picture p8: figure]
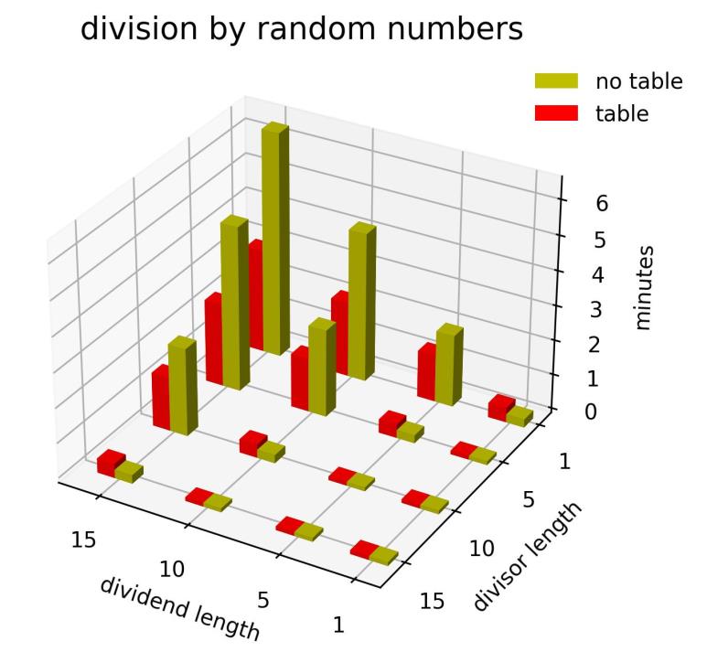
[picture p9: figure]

# Appendix 3: calculating Bernoulli numbers

The most famous and most detailed example of a proposed use for the Analytical Engine, described in Note G of Ada Lovelace’s 1843 translation and expansion of Luigi Menabrea’s paper, was for the computation of Bernoulli numbers. It would be a sublime expression of historical justice if we could demonstrate that computation with our engine.

Lovelace and Babbage never explicitly developed what we today would call the “program” for Bernoulli numbers. Instead, the paper contained a “trace” of the internal state of the machine as the computation proceeded. We need therefore to work backwards from that to the instructions that will induce that behavior. Stephen Wolfram¹¹ has done a helpful analysis of Lovelace’s trace, although he underestimates the time it would have taken to execute. Wolfram, and other¹²,13 useful pages, point out an error, probably typographical, in the fourth line of her trace.

The Lovelace computation used this recurrence relation:

Bn = − ∑(

n
k

)

n−1

k=0

Bk
n + 1 − k
for n>0, with B0=1.

The example she works out in detail is for the calculation of B7, assuming that B1, B3, and B5 have previously been calculated and are in the Store. The computation illustrated in the trace is this, where n=4 for the computation of B2n-1:

B7 = −

1
2

∙

2n − 1
2n + 1

+ B1 ∙

2n
2

+ B3 ∙

2n(2n − 1)(2n − 2)
2 ∙ 3 ∙ 4

+ B5 ∙

(2n(2n − 1)(2n − 2)(2n − 3)(2n − 4) 2 ∙ 3 ∙ 4 ∙ 5 ∙ 6
which she denotes as

B7 = A0 + B1A1 + B3A3 + B5A5

The form of that expression and the trace are more general than is needed to compute just B7, because, as she explains, she is trying to demonstrate part of an imagined more general program that would compute an arbitrarily long sequence of the Bernoulli numbers:

“…we suppose the engine to be in the course of computing the Numbers to an indefinite extent, from the very beginning; and that we merely single out, by way of example, one amongst the successive but distinct series of computations it is thus performing.”

11 “Untangling the Tale of Ada Lovelace”, https://writings.stephenwolfram.com/2015/12/untangling-the-tale-of-ada-lovelace/ (https://writings.stephenwolfram.com/2015/12/untangling-the-tale-of-ada-lovelace/)
12 “Note G”, https://en.wikipedia.org/wiki/Note_G
13 “What Did Ada Lovelace’s Program Actually Do?, https://twobithistory.org/2018/08/18/ada-lovelace-note-g.html

The published trace for computing B7 is generated by executing a total of 36 instructions. It includes two identical iterations of 11 instructions that have been unrolled to create a linear program, since it was designed to be running on the Plan 25 engine that did not include conditional branches or loops.

The trace includes three superfluous instructions to maintain a counter that isn’t actually used. We could remove those, and we could also make minor performance improvements by reusing instead of recalculating some intermediate results.

But for historical authenticity I simulated the calculation of B7 using a program that conforms exactly to the Lovelace trace, except for the correction of the typographical error in step 4. The program below looks like assembly language for the Analytical Engine, but is actually Python code that is executed by the instruction-level simulator described earlier.

decimals=6
scalefactor = 10**decimals
#initial Store variable values come from Number Cards that contain constants

num (V1, 1 * scalefactor) | # 1
num (V2, 2 * scalefactor) | # 2
num (V3, 4 * scalefactor) | # n=4, to compute the 4th number, B(2n-1), or B7
num (V21, int(1/6 * scalefactor)) | # B1, a previously computed Bernoulli number
num (V22, -int(1/30 * scalefactor)) # B3, a previously computed Bernoulli number num (V23, int(1/42 * scalefactor)) # B5, a previously computed Bernoulli number #program: computes B7 = -A0 - A1B1 - A3B3 - A5B5
mul (V2.R, V3.R, [V4,V5,V6]) | #step 1: 2n
sub (V4, | V1.R, V4) | #step 2: 2n-1
add (V5, | V1.R, V5) | #step 3: 2n+1
div (V4, | V5, | V11) | #step 4: (2n-1)/(2n+1)
div (V11, | V2.R, V11) | #step 5: (1/2)((2n-1)/(2n+1))
sub (V13, | V11, | V13) | #step 6: -(1/2)((2n-1)/(2n+1)) = A0
sub (V3.R, V1.R, V10) | #step 7: n-1 counter=3
add (V2.R, V7, | V7) | #step 8: 2 | copy constant
div (V6.R, V7.R, V11) | #step 9: 2n/2 = A1
mul (V21.R, V11.R, V12) | #step 10: A1*B1
add (V12, | V13, | V13) | #step 11: A0+A1*B1
sub (V10, | V1.R, V10) | #step 12: n-2 counter=2
sub (V6, | V1.R, V6) | #step 13: 2n-1
add (V1.R, V7, | V7) | #step 14: 2+1 = 3
div (V6.R, V7.R, V8) | #step 15: (2n-1)/3
mul (V8, | V11, | V11) | #step 16: (2n/2)*((2n-1)/3)
sub (V6, | V1.R, V6) | #step 17: 2n-2
add (V1.R, V7, | V7) | #step 18: 3+1 = 4
div (V6.R, V7.R, V9) | #step 19: (2n-2)/4
mul (V9, | V11, | V11) | #step 20: (2n-2)*((2n-1)/3)*((2n-2)/4) = A3
mul (V22.R, V11.R, V12) | #step 21: A3*B3
add (V12, | V13, | V13) | #step 22: A0+A1*B1+A3*B3
sub (V10, | V1.R, V10) | #step 23: n-3 | counter= 1
sub (V6, | V1.R, V6) | #step 13: 2n-1
add (V1.R, V7, | V7) | #step 14: 2+1 = 3
div (V6.R, V7.R, V8) | #step 15: (2n-1)/3

mul (V8, | V11, | V11) | #step 16: (2n/2)*((2n-1)/3)
sub (V6, | V1.R, V6) | #step 17: 2n-2
add (V1.R, V7, | V7) | #step 18: 3+1 = 4
div (V6, | V7, | V9) | #step 19: (2n-2)/4
mul (V9, | V11, | V11) | #step 20: (2n-2)*((2n-1)/3)*((2n-2)/4)= A3
mul (V23.R, V11, | V12) | #step 21: A3*B3
add (V12, | V13, | V13) | #step 22: A0+A1*B1+A3*B3
sub (V10, | V1.R, V10) | #step 23: n-4 | counter = 0
add (V13, | V24, | V24) | #step 24: A0+A1*B1+A3*B3+A5*B5 = B7
add (V1.R, V3, | V3) | #step 25: n=5 ready to compute B9!
stop ()

43 instructions were executed in 26.8 minutes, using 6 fraction decimals, without tables B7 is 0.033332

Note important constraints on this and all programs for the Analytical Engine:

- There are two types of access encoded on the variable cards: destructive readout (which Lovelace called “Zero Supply-cards”) that leaves the accessed variable zero, and non-destructive readout (“Retaining Supply-cards”) that restores the original value. We denote the latter by appending “.R” to the variable name.
- Variables used as destinations must be zero, or else the result of the computation will be added (digit-by-digit without carries!) to the current value and will be useless. Destination variables generally become zero because their last use was as an operand accessed with destructive readout, so it is important for many of the variable references that they do not include “.R”.
- Since the engine only does fixed point calculations, all the numbers are assumed to have an implied decimal point that is d positions from the right end. For running on the real engine, that number will need to be set by hand on a special figure wheel of a particular axis, which is a procedure that Babbage endorsed. It is used in multiplication to shift d digits off the right of the product, and in division to continue cycling for an additional d digits.

The program above was executed with d=6 digits to the right of the decimal point. I have also measured how long it takes for different values of d, with and without using precomputed tables for multiplication and division.

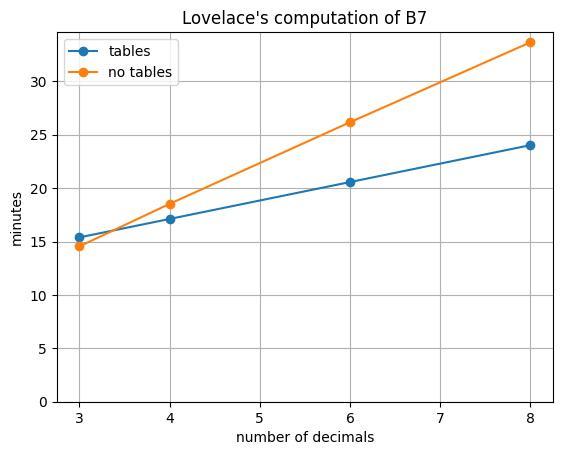
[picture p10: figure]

For this calculation we clearly take a performance hit for not using tables, but the results are nevertheless encouraging. This is definitely a program we will want to run sometimes.

But computing B7 probably takes too long to use for the regular public demonstrations. So I also modeled computing two of the earlier Bernoulli numbers by truncating and simplifying the formula and the program, although for generality it is still written assuming n is a variable.

With n=3, this equation computes B5:

B5 = −

1
2

∙

2n − 1
2n + 1

+ B1 ∙

2n
2

+ B3 ∙

2n(2n − 1)(2n − 2)
2 ∙ 3 ∙ 4

which simplifies to

B5 = −

1
2

∙

2n − 1
2n + 1

+ B1 ∙ n + B3 ∙

n(2n − 1)(2n − 2)
3 ∙ 4

With n=2, the simplified version for B3 is:

B3 = −

1
2

∙

2n − 1
2n + 1

+ B1 ∙ n

Here is the timing for computing B3 and B5.

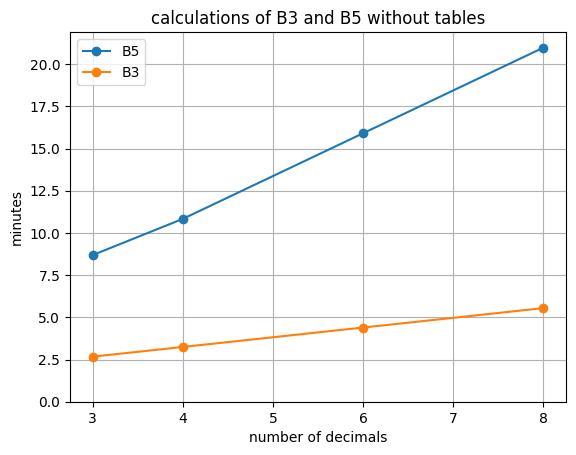
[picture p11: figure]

Either computing B3, or computing B5 with a small number of digits to the right of the decimal point, would make an eminently practical daily public demonstration.

Of course we will create many other demonstration programs (like for the Fibonacci series) that take less time. We will also want some demonstration programs (like for the Greatest Common Divisor) that show off the conditional branching and looping.

# Appendix 4: additional simulated example programs

These example programs are composed of Python statements that mimic an assembly language for the proposed Analytical Engine. They create the Operation and Variable cards that are then input to the instruction-level simulator.

## Compute Fibonacci Numbers

num | (V2, 1) | #constant
num | (V3, howmany) | #how many numbers to compute
num | (V4, 0) | #the previous Fibonacci number
num | (V5, 1) | #the current Fibonacci number
sub | (V7, V3, V7) | #move -count to V7 as loop counter
label("loop")
add | (V4, V5.R, V6) | #compute next number
add | (V5, V4, V4) | #move current to previous
add | (V6, V5, V5) | #move next to current
add | (V7, V2.R, V7) | #increment loop counter
jmpn | (V7.R, "loop") | #jump if not done
stop | ()
52 instructions were executed in 8.3 minutes, using 0 fraction decimals
The last of 10 Fibonacci numbers is 89

## Compute the Greatest Common Divisor of two integers using Euclid’s algorithm

#compute the GCD of V1 and V2 label("loop")

sub | (V1.R, V2.R, V3) #compare a to b
jmpz | (V3.R, "end")
jmpn | (V3,"b_GT_a" )
sub | (V1, V2.R, V1) | #a = a - b
jmp | (V3, "loop")
label("b_GT_a")
sub | (V2, V1.R, V2) | #b = b - a
jmp | (V3, "loop")
label("end")
stop | ()
28 instructions were executed in 3.8 minutes, using 0 fraction decimals The GCD of 27 and 6 is 3

# Appendix 5: component-level simulator

The engine is simulated at a resolution of basic "time units", 15 or 20 of which comprise a "cycle" of the engine. The activities during a cycle are controlled by the current "verticals" on the microprogram barrels, each of which can be thought of as microprogram instruction word.

The model is of an interconnected assembly of hierarchical "components" that have internal state. Examples of components are:
- digit wheels
- stacks of digit wheels
- axles that go through one or more interleaved stacks of digit wheels
- anticipating carriage for an axle
- barrels, and the studs on barrels

Components are created with simple Python function calls:

A = Axle("A",2) #a simple axle with 2 digits per cage
B = Axle("B",2, withcarry=True) #an axle with anticipating carriage Barrel studs are defined, and given semantics that describe their effect on the engine, using calls like these:
create_stud("GIVE_G_TO_C", | lambda barrel: mesh(barrel, G, C))
create_stud("SHR_C_TO_D", | lambda barrel: mesh(barrel, C, D, shift=-1))
create_stud("ADD_A_TO_B", | lambda barrel: mesh(barrel, A, B))
create_stud("SUB_F_FROM_E", lambda barrel: mesh(barrel, F, E, subtract=True))
The “microprogram” on the barrels is then specified by a series of function calls that resemble traditional assembly-language statements with optional labels. The output is a matrix that indicates where on the cylindrical barrel the studs need to be placed. Here is an example program fragment that does unsigned multiplication:

mulpgm = program("multiply program", studnames) #create and assemble the program mulpgm.vertical("outerloop", SHR_C_TO_D, GIVE_C_TO_E)
mulpgm.vertical( | SHL_D_TO_F, GIVE_D_TO_G)
mulpgm.vertical( | SUB_F_FROM_E, GIVE_A_TO_D, CYCLE20)
mulpgm.vertical("innerloop", GIVE_D_TO_A, DECR_E, CYCLE20, IF_RUNUP_EC, "doadd")
mulpgm.vertical("doadd", | ADD_A_TO_B, GIVE_A_TO_D, CYCLE20, "innerloop")
mulpgm.vertical( | SHL_A_TO_D)
mulpgm.vertical( | GIVE_D_TO_A, ADD_G_TO_E, GIVE_G_TO_C, CYCLE20, IF_NORUNUP_EC, "zero_e")
mulpgm.vertical("zero_e", | ZERO_E, "outerloop")
The simulated execution can produce various levels of diagnostic tracing information, or just the results at the end:

multiplying 123456 by 123456
done in 1547 time units, or 4.05 minutes
product is 15241383936

# Appendix 6: document change log

V0.1 | 29 Aug 2023 | L. Shustek | Proposal for a complete but simplified engine
V0.2 | 7 Dec 2023 | L. Shustek | Reframe it as a “prototype Babbage-like” engine that anticipates a subsequent complete Plan xx build
V0.3 | 30 Dec 2023 | L. Shustek | Changes from T Robinson; add explanatory footnotes, add Bernoulli example; implement implied decimals; add unconditional jumps; add link to simulation video; adjust Fusion/360 price; editorial changes from D. Wilborn; more about my simulators.
V0.4 | 8 Jan 2024 | L. Shustek | Restructure into two halves to be more accessible to readers who are not part of the project; add the Executive Summary and sections describing more context for the project.
V0.5 | 4 Feb 2024 | L. Shustek | Changes from G Saviers, T. Robinson; wordsmithing/reordering; don’t call it “prototype”, because we use that to refer to test pieces; more detail on component simulator; position this as a separate but collaborative project relative to Plan28.org.

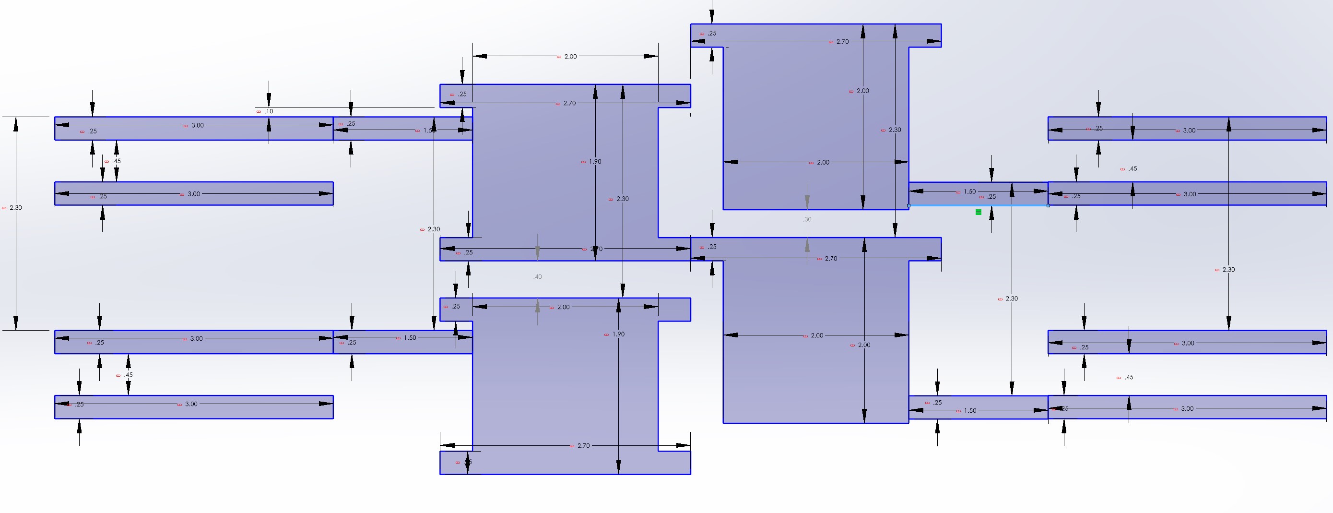
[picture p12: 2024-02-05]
test_designs/mill/3inch_design_elevation.jpg

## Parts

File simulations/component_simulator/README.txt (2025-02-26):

25 Feb 2025
The component simulator now models all the individual gears of digit wheel and pinions, and how they mesh.
It implements microprogram "barrels" that encode programs for both multiplication and division,
using a slightly simplified version of Babbage's Plan 27 layout. It actually computes correct results!

A component-level simulator for the small Babbage Analytical Engine
-------------------------------------------------------------------

The engine is simulated at a resolution of basic "time units", 15 or 20 of which comprise a "cycle" of the engine. 
The activities during a cycle are controlled by the current "verticals" on the microprogram barrels, each of which can be thought of as microprogram instruction word.

The model is of an interconnected assembly of hierarchical "components" that have internal state. 

Examples of components are:
   -	digit wheels
   -	stacks of digit wheels
   -	axles that go through one or more interleaved stacks of digit wheels
   -	anticipating carriage for an axle
   -	barrels, and the studs on barrels
   
Components are created  with simple Python function calls:
    A =  Axle("A",2)  #a simple axle with 2 digits per cage
    B =  Axle("B",2, withcarry=True) #an axle with anticipating carriage
    
Barrel studs are defined, and given semantics that describe their effect on the engine, using calls like these:

   create_stud("GIVE_G_TO_C",   lambda barrel: mesh(barrel, G, C))
   create_stud("SHR_C_TO_D",    lambda barrel: mesh(barrel, C, D, shift=-1)) 
   create_stud("ADD_A_TO_B",    lambda barrel: mesh(barrel, A, B))
   create_stud("SUB_F_FROM_E",  lambda barrel: mesh(barrel, F, E, subtract=True))
   
The “microprogram” on the barrels is then specified by a series of function calls that resemble traditional assembly-language statements with optional labels.
The output is a matrix that indicates where on the cylindrical barrel the studs need to be placed. 
Here is an example program fragment that does unsigned multiplication:

   mulpgm = program("multiply program", studnames) #create and assemble the program
   mulpgm.vertical("outerloop",  SHR_C_TO_D, GIVE_C_TO_E)
   mulpgm.vertical(              SHL_D_TO_F, GIVE_D_TO_G)
   mulpgm.vertical(              SUB_F_FROM_E, GIVE_A_TO_D, CYCLE20) 
   mulpgm.vertical("innerloop",  GIVE_D_TO_A, DECR_E, CYCLE20, IF_RUNUP_EC,  "doadd")
   mulpgm.vertical("doadd",      ADD_A_TO_B, GIVE_A_TO_D, CYCLE20,  "innerloop")
   mulpgm.vertical(              SHL_A_TO_D)
   mulpgm.vertical(      GIVE_D_TO_A, ADD_G_TO_E, GIVE_G_TO_C, CYCLE20, IF_NORUNUP_EC,  "zero_e")
   mulpgm.vertical("zero_e",     ZERO_E,  "outerloop")
   
The simulated execution can produce various levels of diagnostic tracing information, or just the results at the end:
   multiplying 123456 by 123456
   done in 1547 time units, or 4.05 minutes
   product is 15241383936 

For more information see the comment blocks at the start of the source code files.

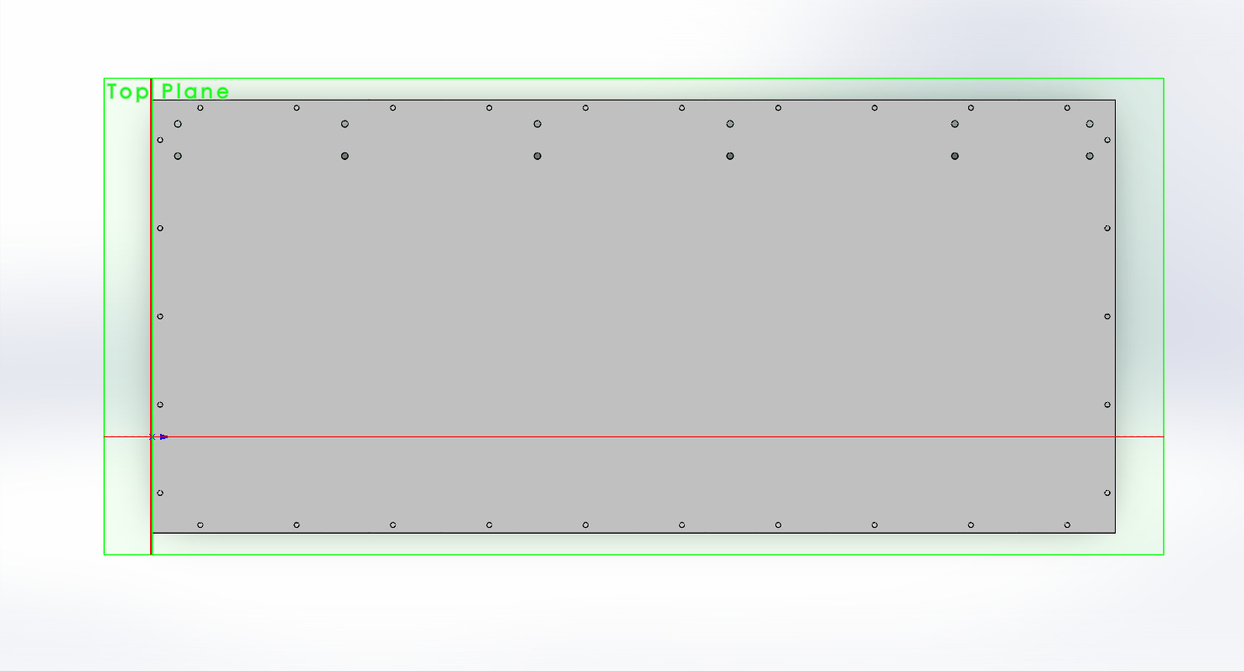
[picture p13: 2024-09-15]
Piers_Plummer_DE/parts/Base_plate.JPG

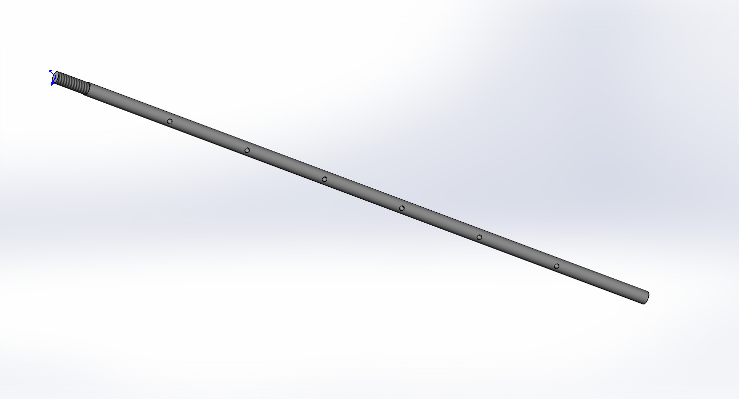
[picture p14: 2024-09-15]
Piers_Plummer_DE/parts/Knife_shaft.JPG

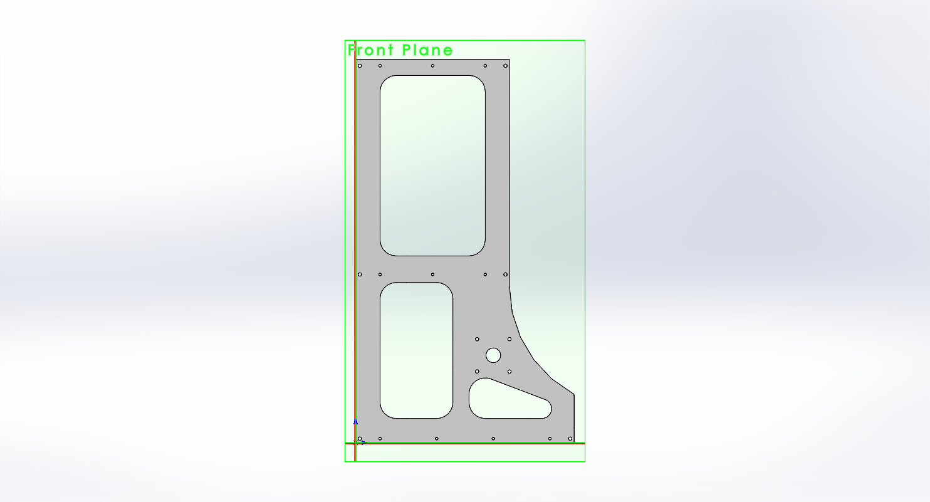
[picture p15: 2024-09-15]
Piers_Plummer_DE/parts/End_plate.JPG

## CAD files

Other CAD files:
Piers_Plummer_DE/assemblies/Frame_assy.SLDASM
Piers_Plummer_DE/parts/Base_plate.SLDPRT
Piers_Plummer_DE/parts/Fig_Crank.SLDPRT
Piers_Plummer_DE/parts/End_bar.SLDPRT
Piers_Plummer_DE/parts/Digit_window.SLDPRT
Piers_Plummer_DE/parts/Bush_flanged_10_13_10_groove.SLDPRT
Piers_Plummer_DE/parts/Window_shaft.SLDPRT
Piers_Plummer_DE/parts/Knife.SLDPRT
Piers_Plummer_DE/parts/Bottom_plate.SLDPRT
Piers_Plummer_DE/parts/Dowel_3_36.SLDPRT
Piers_Plummer_DE/parts/Bush_flanged_6_10_10_groove.SLDPRT
Piers_Plummer_DE/parts/Gear_80mm_40T.SLDPRT
Piers_Plummer_DE/parts/Clevis_M6.SLDPRT
Piers_Plummer_DE/parts/Fig_wheel_zero_alt1.SLDPRT
Piers_Plummer_DE/parts/Fig_axis_shaft.SLDPRT
Piers_Plummer_DE/parts/Knife_shaft.SLDPRT
Piers_Plummer_DE/parts/Bearing_flanged_20_27_4.SLDPRT
Piers_Plummer_DE/parts/Dowel_2_12.SLDPRT
Piers_Plummer_DE/parts/Bearing_30_37_4.SLDPRT
Piers_Plummer_DE/parts/Dowel_1-5_14.SLDPRT
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

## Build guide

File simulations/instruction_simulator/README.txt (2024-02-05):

An instruction-level simulator for the small Babbage Analytical Engine
----------------------------------------------------------------------

An AE program is created by writing a series of Python function calls that resemble 
traditional assembly-language statements, like these:
   
     add   (V1, V2, V3)       #add axis 1 to axis 2 and put the result on axis 3
     jmpz  (V4, "somewhere")  #if the value on axis 4 is zero, jump to "somewhere"
     
The result is an internally-generated loop of Operation Cards, and another of Variable Cards.
It can also generate a series of Number Cards for entering constants into the Store, but
they cannot be looped or repeated.

The program on the cards can be displayed for checking with the function "disassemble()".

The program can be run on a simulated engine with the function "run()". By default it generates
a trace of the relevant internal machine state as it executes, and then displays some statistics
when it stops.

Once we define the format of the cards, we can add a function that will draw (or even punch, 
given a connection to an appropriate device) the cards, which then can be stitched into 
loops and loaded onto the reading prisms of the engine.

--- the assembler language specification, by example ---

Dyadic instructions generate one operation card and three variable cards

    add (V1, V2, V3)      # V1+v2 --> V3
    sub (V1, V2, V3)      # normally operands are read destructively and become zero, but
    mul (V1.R, V2, V3)    #  appending ".R" makes the access non-destructive ("restoring access")
    div (V1, V2, [V3,V4]) # the destination can be a list of variable axes in the Store

Monadic instructions generate one operation card and two variable cards

    shl (V1, V2)          # shift V1 left one digit (multiply by 10) and put the result in V2
    shr (v1, V2)          # shift V1 right one digit (divide by 10) and put the result in V2

Jump instructions generate one operation card that contains a count and direction of operation cards to skip,
and one variable card that contains the count of variable cards to skip. In both cases the count is relative
to the card following the current one.

    jmp  (V1, "name")    # jump to label "name" (the value of axis V1 is ignored)
    jmpz (V1, "name")    # jump to label "name" if V1 is zero
    jmpn (V1, "name")    # jump to label "name" if V1 is negative (TBD: what about zero?)
    jmpp (V1, "name")    # jump to label "name" if V1 is positive (TBD: what about zero?)
    
The instruction to load a constant from the next Number Card into the location specified on a Variable Card

    num (V1, value)      # load the number card having the specified signed value

Miscellaneous instructions generate only one operation card

    stop ()              # stop the program and the engine

Assembler pseudo-operations and control assignments

    label("name")      # define a location at the next instruction to be the target of jumps
    initialize()       # clear the cards and zero all Store variables
    disassemble()      # show the generated operation and variable cards
    run()              # execute the cards to run the program
    showvariable("the answer", V7) # display a Store variable
    Trace = True       # enable the trace of operations during the run
    decimals = 6       # set the number of implied digits to the right of the decimal point

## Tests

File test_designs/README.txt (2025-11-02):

This directory hints at experiments to create physical examples of parts 
and mechanisms that will be needed for the small Babbage Analytical 
Engine.

I am building a sequence of "prototypes" of increasing complexity. All 
the early versions use stepper motors controlled by a microprocessor to 
do shaft lifting and rotation, as a temporary substitute for what must 
eventually become Babbage-like timing and control using cams.

The first prototype has been built and is operational, a second is under 
construction, and a third is anticipated.

Version 1 had:
   - one 2-number 4-digit register stack
   - one each fixed and movable pinions that can transfer and shift
   - two linking pinions to connect each of those to either register number
   - one anticipating carriage that can add and subtract
   - one linking pinion to connect the fixed pinion to the carriage
   - locks on the digit wheels, long pinions, and carriage

 Here's how they were interconnected:

   C  -- F -- FC -- FP == FPC -- \
                    ||            -- A1 or A2
                    MP == MPC -- /

  Double lines represent axles that are always connected, but the FP==MP
  connection can optionally be from MP to the FP above, which does a shift.
  Connecting both FPC and MPC to the same A digit wheel creates a jam.
  
  The canonical test program, which runs well, computes the Fibonacci series.
  See the video at https://youtu.be/I2eggg87dSU.

Version 2 has all of that and adds:
   - a Store with two 2-number digit stacks, so four memory locations
   - a rack for connecting the Store to the Mill
   - a rack-restoring pinion to return the rack to the home position, and
     optionally rewrite the number just read and set to zero
   - a linking pinion to connect the rack to the movable pinion
   - two 20-digit general-purpose counters that can be linked to each other
   - one single-position sign wheel that receives and transmits the sign wheel
     of Store variables
   - an optional reversing gear between the long pinion and the carriages
   - a "running up" lever at the top of the carriage to detect overflows
   - perhaps, since we've reduced the cage height from 2.3" to 2", there will
     be space for 5 digits in all the mechanisms instead of 4.
     
   Preliminary images and incomplete files for the program that runs the stepper
   motors is in the version2 directory.

Version 3 will have all of that and add:
   - a second set of the 2-number register stack, fixed and movable long pinions,
     and anticipating carriage
   - a third set of the 2-number register stack, and fixed and movable long pinions,
     but not a third anticipating carriage.
   - four more Store stacks, for a total of six stacks (12 numbers)
   
   That configuration is essentially the Plan 27 layout, with some performance-enhancing
   features removed. It will be sufficient to do multiplication and division, and all 
   the user-level instructions we propose to implement.
   
   After that comes: card readers, microcode barrels, and control sequencing.

Len Shustek
2 Nov 2025

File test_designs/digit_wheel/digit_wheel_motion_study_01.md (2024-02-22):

https://github.com/LenShustek/AnalyticalEngine/assets/3602038/6223b28f-ae67-4904-bab0-c1efb5147b36

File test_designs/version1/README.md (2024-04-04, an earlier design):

# Anticipating Carriage tests

One of the inventions that Babbage was most proud of was his
"anticipating carriage", which does the propagation of carries
in a short time that is independent of the number of consecutive
cascading 9's.  Over a period of decades he produced 88 different
designs for it, so we have many to choose from or be inspired by.

This is a blog-like record of design ideas and sketches for it, in reverse chronological order.

## 4 April 2024

The parts have now been made and the carriage tester prototype is assembled; see carriage v2 tester.jpg. Now I can begin debugging.

I'm not optimistic.

## 10 Mar 2024

The prototype for testing the anticipating carriage continues to develop. 

There were some side roads leading to dead ends that wasted several days. I thought the carry warning could be simplified by putting the carriage digit wheel gear adjacent to the carry nib disc, but that doesn't work because when the carry sector engages, it interferes with the movable wire. Then I tried doing away with the big intermediate carry pinion by using the regular fixed long pinion instead, but it too causes interference. So it's basically back to the 29 Feb 2024 design.

What is shown here as V2 is a tester for it that implements addition and subtraction to the anticipating carriage, optionally making a copy of the input onto the second number of the input digit wheel stack. That will be enough mechanism to run a program to compute Fibonacci numbers. The prototype also implements, just for testing in anticipation of what will be needed for multiplication and division, power-of-10 shifting in both directions.

I've started to build the frame for the prototype, and to wire up the electronics for the stepper motors using multiple copies of a PC board I had designed several years ago for automating our weaving loom, https://github.com/LenShustek/loom. But the detailed mechanical design needs to be studied a little more before it's time to start 3D printing the parts. If anyone sees a problem please let me know quickly.

## 29 Feb 2024

I continue to develop the design for the anticipating carriage. See the latest drawing in carriage v1.1.jpg.

In order to do subtraction I came up with a tweak that Babbage apparently never used: rather than having two different numberings on the wheel to change the chain-of-9 detector using the fixed and movable wires into a chain-of-0 detector, I move the detector itself to either the 9-position of the movable wire or the 10-position. This results in a considerable simplification.

There may well be some fatal flaw in this scheme, because surely Babbage would otherwise have proposed it. But so far neither Tim Robinson nor I have discovered the problem. 

I may be ready to build a prototype to try it out. The idea is to build a frame, perhaps 12"W x 18"L x 12"H, to contain the 19th-century mechanism shown in the drawing. Below that will be the 21st-century magic that animates it for testing: 7 stepper motors to provide shaft rotary motions, and 5 to provide shaft lifting motions using lead screws. Plus 12 stepper motor drivers, a microprocessor, and a sprinkling of software.

## 8 Feb 2024

This first experiment (V1) is just an cartoon sketch to see if
I've got the basic idea right. I used Solidworks to draw a 4-digit
stack and some of the required parts. The video is an *animation*, 
not a *simulation*; it doesn't recognize interference or make motion
inferences based on contact between parts.

The animation shows a number (just a single units digit) being added from the stack on the right to the carriage in the center. The actual numerals on the digit wheels are missing, and the relative position of the carry warning tab to the moveable "wire" (actually a slug) that detects the 9 position is arbitrary.

The animation demonstrates a particularly hard case:
- the units digit on the bottom rotates from 9 to 0 and beyond, so it must cause a carry to the tens
- the tens digit is at 9, so it must propagate the carry to the hundreds using the moveable wire
- the hundreds is at 8, so it doesn't propagate, but it must avoid interference of its moveable wire with the carry warning from below

The timing isn't as good as as Babbage achieved:

1. 9 time units for "giving off" of the value on the right stack, which moves the carry warning at the units level into position
2. 1 time unit for raising the carry chain and the pinions that need to increment digit wheels
3. 1 time unit for locking the pinions
4. 1 time unit for lowering the carry chain to avoid interference
5. 1 time unit for rotating the pinions to move the wheels by one digit

We need to do better.

Not shown is the return to the home position, or how to deal with subtraction. There's plenty more to do.

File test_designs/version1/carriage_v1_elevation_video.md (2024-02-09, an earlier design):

https://github.com/LenShustek/AnalyticalEngine/assets/3602038/d959abbe-8713-4ec3-92a2-474ec2440568

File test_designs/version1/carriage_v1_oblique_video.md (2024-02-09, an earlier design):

https://github.com/LenShustek/AnalyticalEngine/assets/3602038/c2837cca-8fb5-47ce-8303-d3551eef4331

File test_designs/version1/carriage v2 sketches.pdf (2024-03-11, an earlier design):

# carriage prototype plan view sketch #1

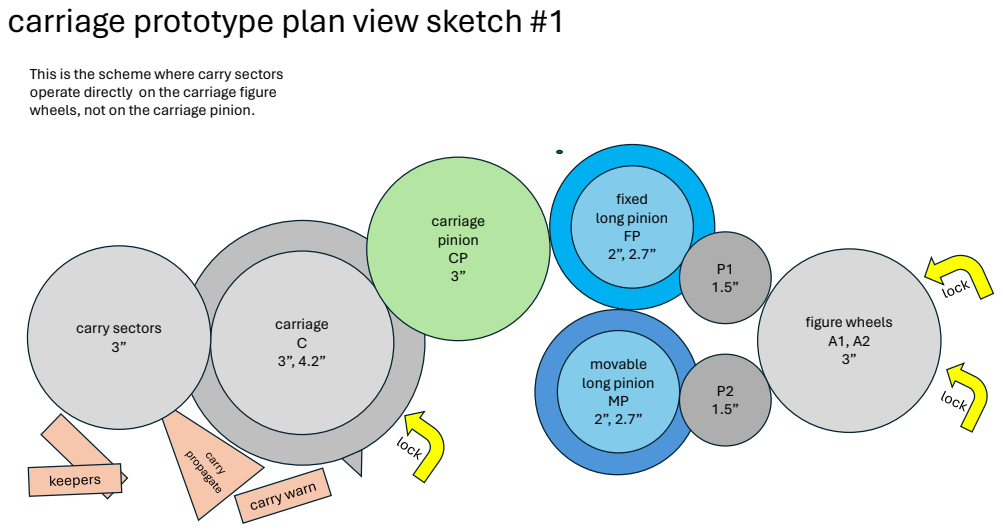
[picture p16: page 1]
fixed long pinion FP 2”, 2.7”; carriage C 3”, 4.2”; figure wheels A1, A2; movable; long pinion MP 2”, 2.7”; carry sectors 3”; carriage pinion CP 3”

This is the scheme where carry sectors
operate directly on the carriage figure
wheels, not on the carriage pinion.

P1

figure wheel A1

figure wheel A2

P2

figure wheel A1

figure wheel A2

## add A1 to C

## and optionally give off A1 to A2

carriage C | carriage pinion CP
fixed long pinion FP | | movable long pinion MP

fixed long pinion
FP

could exchange A1 and A2

## driving

## subtract A1 from C

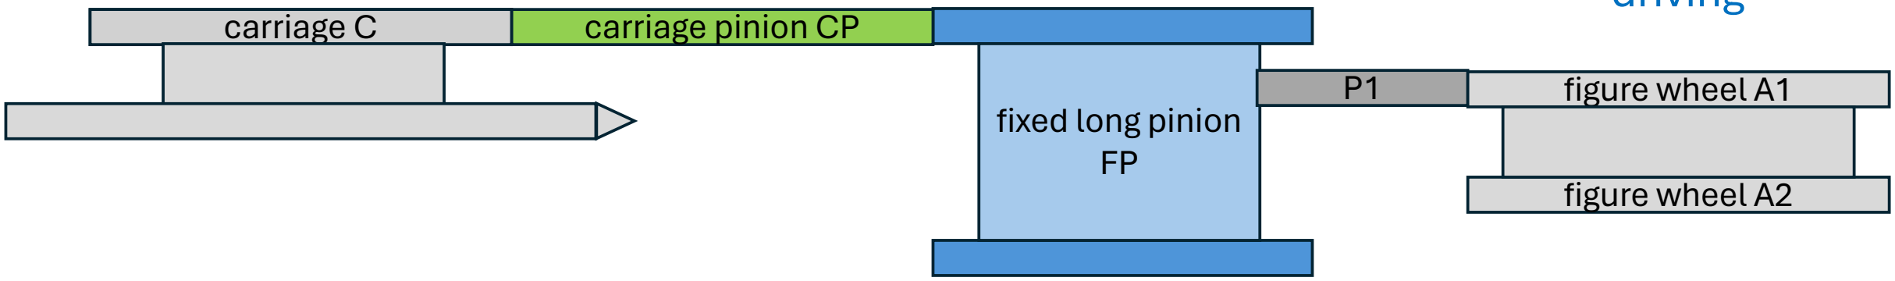
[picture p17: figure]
carriage C; fixed long pinion FP; figure wheel A1; figure wheel A2; carriage pinion CP

## and optionally give off A1 to A2

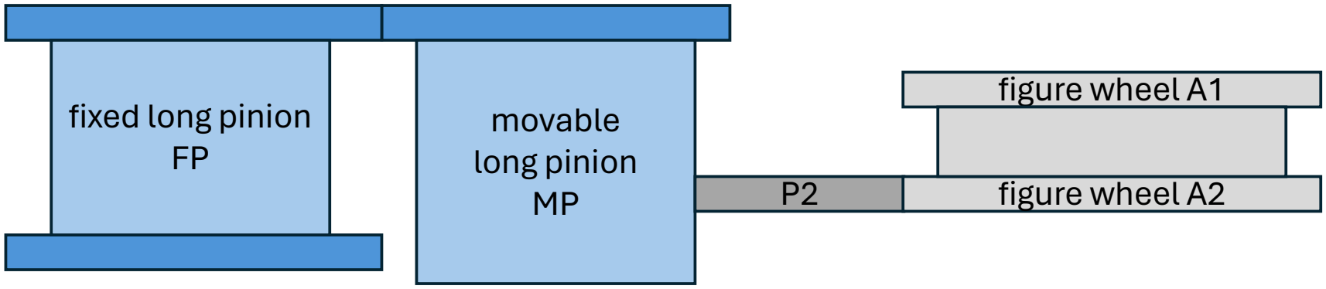
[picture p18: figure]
movable long pinion; figure wheel A1; figure wheel A2; fixed long pinion FP

could exchange A1 and A2

## driving

## give C to A1

could substitute A2 for A1

figure wheel A1

figure wheel A2

P2

carriage C | carriage pinion CP
fixed long pinion FP | | movable long pinion MP

## driving

## shift A1 right to A2 shift A2 left to A1

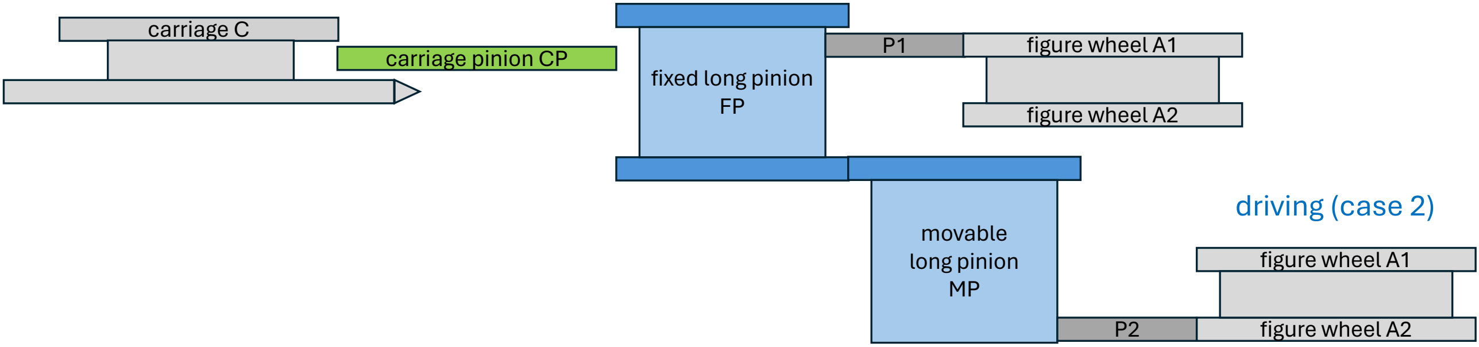
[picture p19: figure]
fixed long pinion FP; figure wheel A1; figure wheel A2; movable long pinion MP; carriage pinion CP; carriage C; driving (case 2)

could exchange A1 and A2

## driving (case 1)

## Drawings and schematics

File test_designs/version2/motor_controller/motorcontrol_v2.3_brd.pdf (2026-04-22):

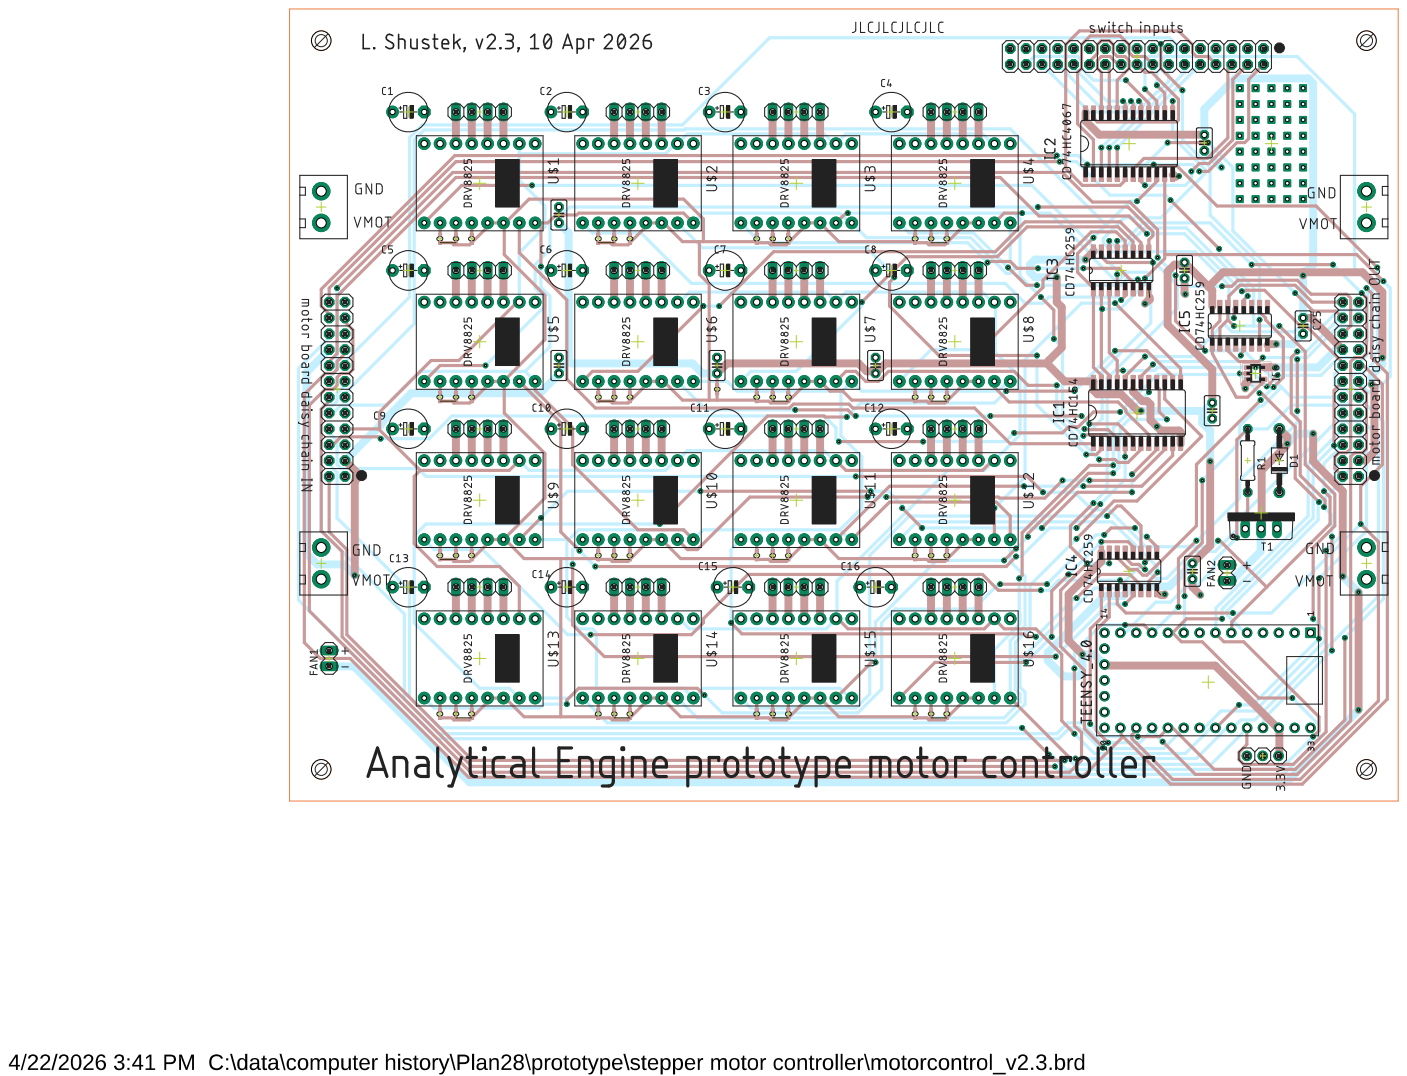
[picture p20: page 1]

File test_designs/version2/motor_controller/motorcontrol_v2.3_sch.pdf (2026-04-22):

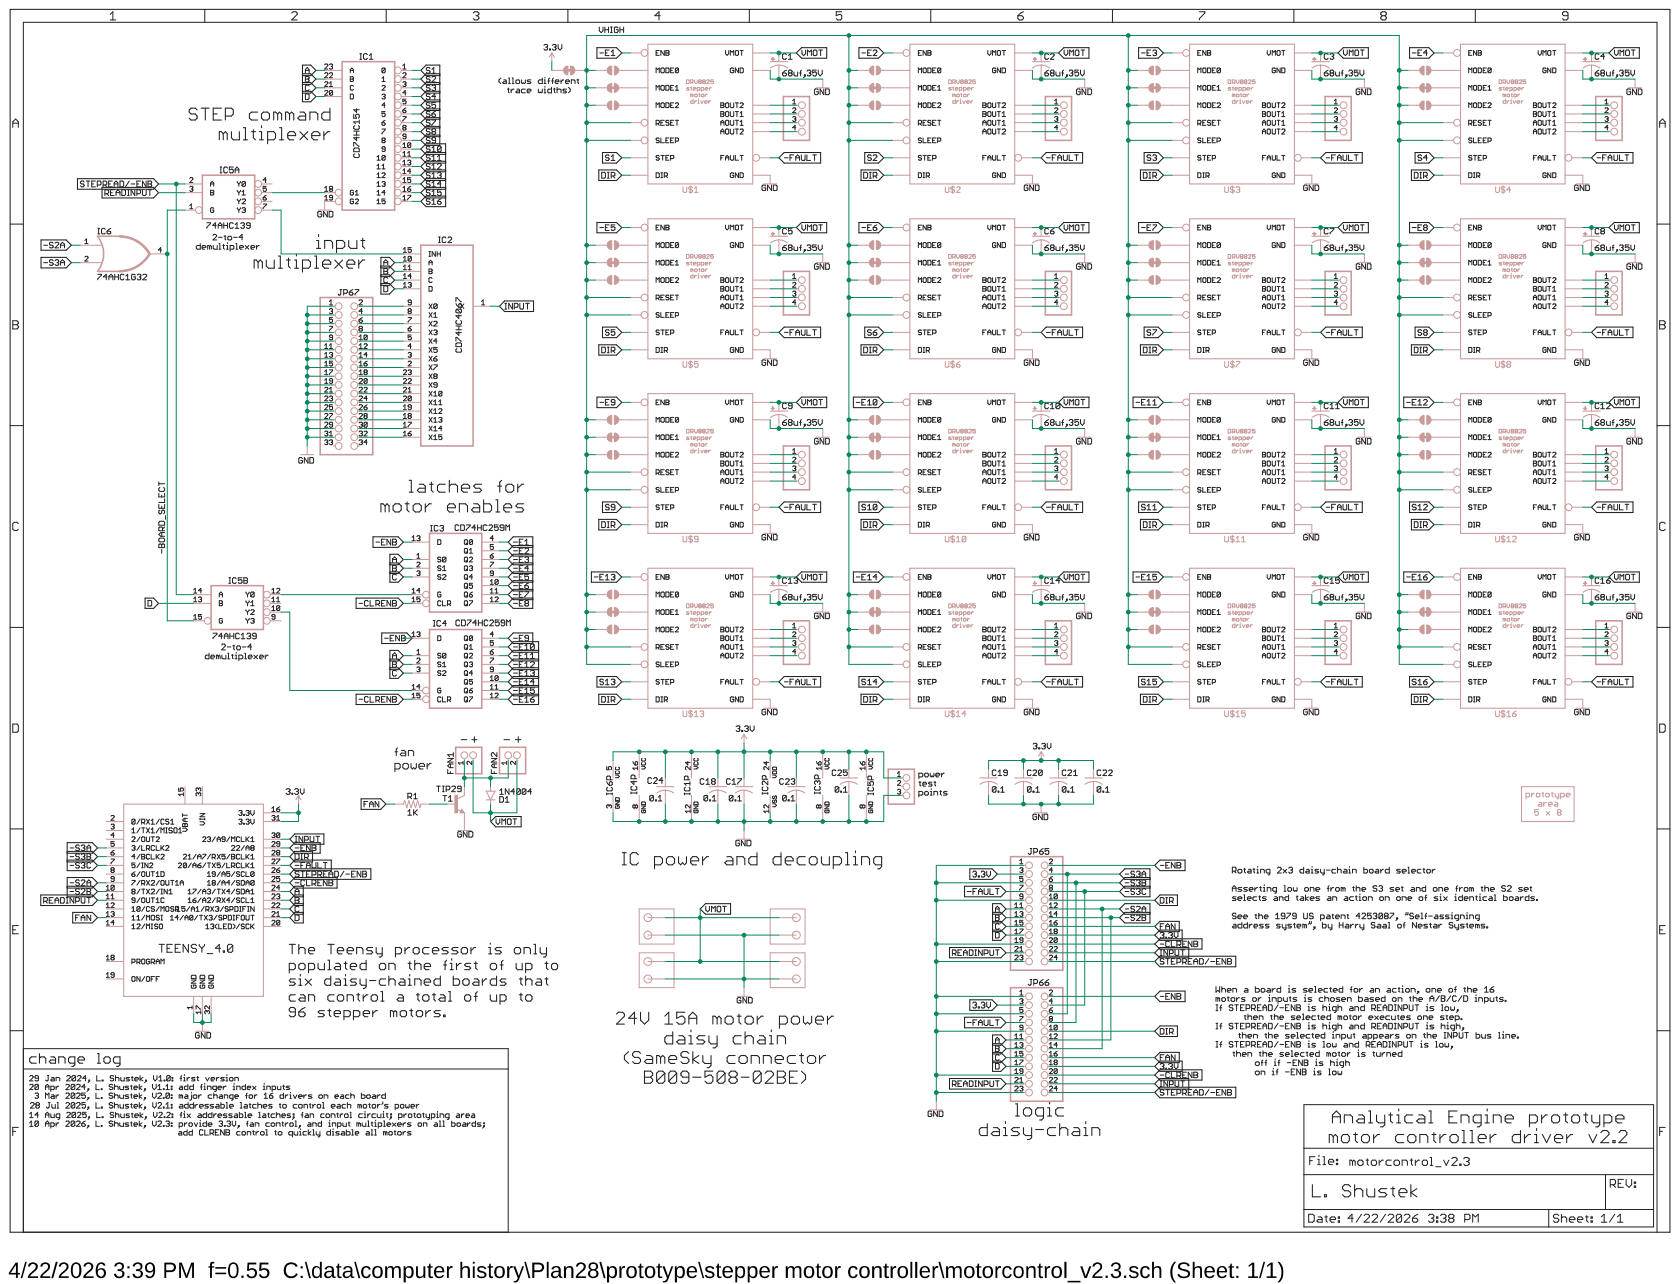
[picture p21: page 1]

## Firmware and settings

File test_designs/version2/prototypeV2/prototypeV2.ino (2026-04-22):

#include "prototype.h"
#include "EEPROM.h"
/***********************************************************************************************************

   -----  Control program for the Analytical Engine prototype  -----

   The AE prototype is a testbed for some Babbage-designed 19th century mechanisms.
   It is driven for testing from the level below by 21st century stepper motors and
   electronics. This is the control program for its Teensy 4.0 microcomputer.


   There are three version of the "prototype", in addition to some special testers.

   Version 1 had:
      - one 2-number 4-digit register stack
      - one each fixed and movable pinions that can transfer and shift
      - two linking pinions to connect each of those to either register number
      - one anticipating carriage that can add and subtract
      - one linking pinion to connect the fixed pinion to the carriage
      - locks on the digit wheels, long pinions, and carriage

    Here's how they were interconnected:

      C  -- F -- FC -- FP == FPC -- \
                       ||            -- A1 or A2
                       MP == MPC -- /

     Double lines represent axles that are always connected, but the FP==MP
     connection can optionally be from MP to the FP above, which does a shift.
     Connecting both FPC and MPC to the same A digit wheel creates a jam.

   Version 2 has all of that and adds:
      - a Store with two 2-number digit stacks, so four memory locations
      - a rack for connecting the Store to the Mill
      - a rack-restoring pinion to return the rack to the home position, and
        optionally rewrite the number just read and set to zero
      - a linking pinion to connect the rack to the movable pinion
      - two 20-digit general-purpose counters that can be linked to each other
      - one single-position sign wheel that receives and transmits the sign wheel
        of Store variables
      - an optional reversing gear between the long pinion and the carriages
      - a "running up" lever at the top of the carriage to detect overflows
      - perhaps, since we've reduced the cage height from 2.3" to 2", there will
        be space for 5 digits in all the mechanisms instead of 4.

   Version 3 will have all of that and add:
      - a second set of the 2-number register stack, fixed and movable long pinions,
        and anticipating carriage
      - a third set of the 2-number register stack, and fixed and movable long pinions,
        but not a third anticipating carriage.
      - four more Store stacks, for a total of six stacks (12 numbers)
   This configuration is essentially the Plan 27 layout. It will be sufficient to do
   multiplication and division, and all the user-level instructions we propose.

   The motors are controlled by the microcomputer as directed by motion commands entered
   on a USB serial console. All commands take one unit of "timeunit" milliseconds by default,
   except that "lock" and "unlock" takes half that. The defaults can be overridden with the
   "time" command modifier.

   This version of the software corresponds to Version 2 described above.

   The serial console should be set for "newline" as the ending character.
   We use the Coolterm terminal emulator because the Arduino Serial Monitor
   doesn't provide for reading individual characters until Enter has been hit.
   Use these Options: "Enter key is LF", and "Handle BS and DEL".

   Several commands can be on one line, separated by semicolons.
   Hitting "Enter" on an empty line repeats the last command.
   Hitting "backspace" on an empty line repeats the next-to-last command.
*/
const char* help[] = { // COMMANDS
   // These are the 19th century engine action commands
   " lock|unlock An top|bot, MPn, FPn, R", // move a gear lock in 1/2 timeunit
   " lock1 MPn, FPn",                          // lock only the top (MP) or bottom (FP) pinion
   " mesh FPn|MPn An top|bot, Sn|RR top|bot rack|finger, SIGN rack|finger, RPn An top|bot, RPn MPn, FCn, REVn in|lock",
   " unmesh FPn|MPn An, Sn, RR, SIGN, RPn, FCn, REVn", // break that link
   " finger An top|bot, Fn",                // make the giving-off finger engage with the named digit wheel
   " nofinger An, Fn",                         // make the giving-off finger not engaged
   " shift MPn [up|down]",                    // make the movable long pinons shift, or not
   " giveoff An|Fn|Sn|RR|SIGN [degrees] [reverse]",// rotate the digit wheel down (or up) one digit, or an arbitrary degrees
   " setcarry Fn 0|9",                        // carry chain position for 0's or 9's
   " carrywarn Fn up|down|reset|return",      // carry warning arm lift, or rotate to reset the carry warning arms
   " carry Fn add|sub|home",                  // rotate the carry sectors to add or subtract one, and return to home position
   " keepers Fn up|mid|down|top|bottom",      // lift or rotate the carry sector keepers into position
   " switchtest <name>",                      // test a named switch; set stop_repeat if on
   " testmotor b n",                          // test motor n on board b
   "+optional: delay | time n m",             // for movements: delay to 2nd half, or to time relative to 0..99

   // these are the 21st century driver commands
   " [run]|step %s",                           // run or single-step a script, with #n replaced with the nth parm
   "   read|write Sn top|bot Am top|bot",      // read or write between Store n and Mill m
   "   readonly Sn top|bot",                   // read Store s
   "   restore read|write",                    // restore the rack after reading or writing
   "   rewrite Sn top|bot",                    // restore the rack after reading and rewrite the value
   "   zero Sn|An|Fn|RR|SIGN top|bot [calibrate]", // zero (or maybe calibrate) a digit stack
   "   set Sn|An top|bot",                     // set a digit stack by hand
   "   add|sub|load An top|bot",               // mill digit wheel: add it to, subtract it from, or load it from its carriage
   " repeat [n] <commands>",                   // repeat a list of commands until count or /

   // All those are remembered and can be repeated with Enter or Backspace.
   // The following state commands are not remembered:
   " home | state | reset | pause [ms|comment] | bell | restart",  // move to initial position, show state, reset internal state, pause script n msec, sound bell, restart processor
   " timeunit [ms] | tu | debug [n]",     // set parameters
   " switches | motors",                  // monitor for changes in the switches; show motor assignments
   " help | ?",                           // show help
   " off|on <axle>",                      // motor power control for either everything or a named axle motor
   " rot|lift <axle> <amount>",           // primitive lift in mils, or rotation in degrees
   " calibrate <axle> <degrees>",         // force calibration of digit wheel stack
   NULL };
/*
   When movements are in progress:
     - hitting ESC does an emergency abort with no further motion
     - hitting any other character does an abort and then a "home" command

   Information about the digit wheel rotational position sensors that has been deduced by
   "calibrate" commands is recorded in non-volatile EEPROM memory and loaded on startup.

   Except for the rotational position of the finger axles that is sensed by a microswitch and
   can be initialized with the "zero" command, the machine cannot sense its current physical
   state. It assumes the following initial conditions on startup or after a "reset" or "home"
   command is issued:

      lock F; lock A1; lock A2; lock FP; lock MP;
      unmesh FC; unmesh FPC; unmesh MPC; unmesh REV; 
      nofinger F; nofinger A
      setcarry 9; carrywarn down;
      keepers top; keepers down
      //carry sectors rotated towards F
      //carry warning arms set to "not warned"
      ...MORE TBD...

   Set the reference voltage on the DRV8825 driver boards to current limit as follows:
     NEMA 17 60mm long: max 2.1A, set to 0.8V for 1.6A
     NEMA 11 28mm long: max 0.8A, set to 0.4V for 0.8A
     NEMA 8  39mm long: max 0.8A, set to 0.3V for 0.6A
     NEMA 8  27mm long: max 0.2A, set to 0.1V for 0.2A

   To further limit torque on certain motors, lower the reference voltage, or increase torque with higher voltage.

   We use quarter-step micro-stepping, so the holding torque is reduced to about 38%
   compared to full stepping. But apparently pull-out torque is not; see these:
   See https://embeddedtronicsblog.wordpress.com/2020/09/03/torque-vs-microstepping/
   and https://www.rototron.info/wp-content/uploads/PiStepper_Microstepping_WP.pdf.

   ---- change log ----
   14 Mar 2024, L. Shustek, started, compatible with Teensy 3.5, 3.6, or 4.1.
   19 May 2024, L. Shustek, various changes and additions
   17 Jun 2024, L. Shustek, add carriage wire return motors
   26 Sep 2024, L. Shustek, add fixed long pinion lock, and option for small prototype tester
    1 Oct 2024, L. Shustek, add partial time unit operations so that 2 consecutive locks can occur in 1 unit
   19 Oct 2024, L. Shustek, change to new bidirectional carry warning arms that can lower the carry sector lifters;
                            add half cycle unlocks; change some command terminology
   27 Oct 2024, L. Shustek, add carry sector lifter return arms rotated by a new motor
    5 Nov 2024, L. Shustek, remove that new motor for the new carry lifter design, so we're back to 17
    9 Dec 2024, L. Shustek, implement "time n m" to allow movements to span multiple time units
    5 Feb 2025, L. Shustek, add "nolock" for weak locking of F locks
   16 Apr 2025, L. Shustek, Support the new version 2 motor control boards.
                            Implement exact motor movement by accumulating fractional microstep deficits.
                            Support the store tester jig.
   31 Jul 2025, L. Shustek, Retrofit to work with add/sub (Fibonacci) prototype again.
   19 Aug 2025, L. Shustek, Major change for store/add/sub prototype. Divide into multiple modules.
   31 Aug 2025, L. Shustek, Allow parallel execution of scripts; add script substitutable parameters
    2 Nov 2025, L. Shustek, Allow some motors to round down movements to full steps to allow powering down.
   16 Apr 2026, L. Shustek, Add a line editor for commands; add testmotor
   *************************************************************************************************************/

struct config_t  // the configuration record written to non-volatile EEPROM memory
   config = { 0 };

unsigned long timeunit_usec = DEFAULT_TIMEUNIT_MSEC * 1000L;  // to move one digit, or lift, or unlock, etc.

int debug = 2;              // debug level from 0 to 5
int motors_queued = 0;      // how many motors are currently queued up to move
bool got_error = false;     // was an error generated during this action?
bool script_step = false;   // should we pause at each script command?
int cyclenum = 0, totaltime = 0;

void assert(bool t, const char *msg, ...) {
   if (!t) {
      va_list args;
      va_start(args, msg);
      Serial.print("*** ASSERTION FAILED  ");
      char line[200];
      vsnprintf(line, sizeof(line), msg, args);
      Serial.println(line);
      va_end(args);
      while (1); } }

void read_config(void) {
   for (unsigned i = 0; i < sizeof(config); ++i)
      ((char*)&config)[i] = EEPROM.read(i);
   if (strncmp(config.id, CONFIG_ID, sizeof(config.id)) != 0)
      Serial.printf("*** no config block in EEPROM\n");
   else for (int motornum = 0; motornum < NUM_MOTORS; ++motornum)
         if (config.finger_zero_degrees[motornum].degrees != -1) { // undefined is 0xff!
            struct motord_t *pmd = motor_num_to_descr[motornum];
            assert(pmd, "undeclared motor: %d", motornum);
            Serial.printf("digit wheel %s (%s) is calibrated to %d degrees\n",
                          pmd->axle_name, pmd->axle_descr,
                          config.finger_zero_degrees[motornum].degrees); } }

void write_config(void) {
   strcpy(config.id, CONFIG_ID);
   for (unsigned i = 0; i < sizeof(config); ++i)
      EEPROM.write(i, ((char*)&config)[i]);
   Serial.printf("config block written\n"); }

void setup(void) {
   initialize_iopins();  // disable all motor controllers quickly
   Serial.begin(115200);
   delay(500);
   while (!Serial.available())
      ;  // wait for terminal emulator to connect and user to hit Enter
   Serial.printf("*** AE prototype tester ***\nThe timeunit is %d msec, debug is %d.\n", timeunit_usec / 1000L, debug);
   initialize_motors();
   read_config(); }

//****  the main loop

void loop(void) {

   getcmdline();  // get a command line from the keyboard
   got_error = script_step = false;
   cyclenum = totaltime = 0;
   execute_commands(cmdline);
   //if (!got_error) do_movements(timeunit_usec);  // do any queued "rot" and "lift" movements
   if (cyclenum > 1) {
      unsigned msec = totaltime / 1000;
      Serial.printf("%u time units, %u.%03u seconds, %u msec per time unit\n", 
      cyclenum, msec / 1000, msec % 1000, msec/cyclenum); } }

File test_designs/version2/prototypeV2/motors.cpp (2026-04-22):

#include "prototype.h"

#define MIN_uSTEP_TIME_USEC 250  // minimum time between microsteps for reliable operation
// 1000 RPM max * 800 usteps/rev * min/60 sec = 75 usec, but 100 usec doesn't work!
#define MOVE_TICK_USEC 50       // how often to wait between check for something to do when moving
#define STEPS_PER_ROTATION 200  // 1.8 degree step angle for Nema 11 2-phase stepper motor

/* The default for lifters is no gearing, ie 1:1, because most of them drive a leadscrew directly.
   The default for rotators is the "5:1" gearmotor sold by StepperOnline, also described as "5.18:1".
   The actual ratio is 5+2/11, or 5.1818181818, which we rationalize as 57/11.
   For more info, see the comments in queue_movement(). */
#define GEARMOTOR_BIG 57  // 57:11 gearing in the gearmotor
#define GEARMOTOR_SMALL 11
#define MILL_DIGIT_GEAR_BIG 2  // 32:16 (2:1) gearing in the Mill
#define MILL_DIGIT_GEAR_SMALL 1
#define STORE_DIGIT_GEAR_BIG 25  // 50:16 (25:8) gearing in the Store
#define STORE_DIGIT_GEAR_SMALL 8

//**** define I/O pins

#define MOTOR_BDSEL_2A 7  // board select: make one of 2A/2B low and one of
#define MOTOR_BDSEL_2B 8  // 3A/3B/3C low to select one of six identical motor
#define MOTOR_BDSEL_3A 3  // control boards that are daisy-chained together.
#define MOTOR_BDSEL_3B 4  // See the 1979 patent 4,253,087, "Self-assigning address
#define MOTOR_BDSEL_3C 5  // system", by Harry Saal of Nestar Systems

#define MUXA 17        // 4-to-16 multiplexer controls for addressing the motors
#define MUXB 16        //   on the currently-selected board,
#define MUXC 15        //   or for reading one of the 16 global switch inputs
#define MUXD 14        //
#define STEPnotENB 19  // whether selecting the board steps the motor selected by the ABCD
//                      //   multiplexer, or sets the power on/off status of that motor
#define MOTOR_ENB 22  //   depending on the state of MOTOR_ENB
#define MOTOR_ON LOW
#define MOTOR_OFF HIGH
#define SWITCH_INPUT 23  // input: the switch selected by the A/B/C/D mux controls

#define MOTOR_FAULT 20  // active low input: a motor fault was detected
#define MOTOR_DIR 21    // direction control for all motors
#define FAN_ON 11       // turn on the cooling fans

#define HIGH 1
#define LOW 0

struct switchnum_t switch_numbers[] = {  //map from switch number to switch name
   { SW_A2, "A2" },
   { SW_F2, "F2" },
   { SW_CTR2, "CTR2" },
   { SW_CTR1, "CTR1" },
   { SW_RR, "RR" },
   { SW_S1, "S1" },
   { SW_S2, "S2" },
   { SW_SIGN, "SIGN" },
   { F2_RUNUP, "RUNUP" },
   { 0, NULL } }; // end marker

int num_declared = NUM_MOTORS, num_defined = 0, num_assigned = 0;

struct motor_select_t {  // map from motor number 0 to 95 to I/O pins needed to select it
   int bd_grp2;           // which of MOTOR_BDSEL_2A/2B to assert to select the board
   int bd_grp3;           // which of MOTOR_BDSEL_3A/3B/3C to assert to select the board
   int motorpos;          // which motor position on that board labeled from 0 to 15
} motor_selects[NUM_MOTORS];
int motorboards[6][2] = {              // outputs that select each of the six boards
   { MOTOR_BDSEL_2A, MOTOR_BDSEL_3A },  // The 0th board, with the Teensy processor.
   { MOTOR_BDSEL_2B, MOTOR_BDSEL_3B },  // The remaining boards in the order of
   { MOTOR_BDSEL_2A, MOTOR_BDSEL_3C },  // the daisy chained cables, connected from
   { MOTOR_BDSEL_2B, MOTOR_BDSEL_3A },  // the right connector of one board to the
   { MOTOR_BDSEL_2A, MOTOR_BDSEL_3B },  // left connector of the next board.
   { MOTOR_BDSEL_2B, MOTOR_BDSEL_3C } };
void setmotor(enum motornum_t motornum /*0 to NUM_MOTORS-1*/, int boardnum /*1 to 6*/, int motorposn /*1 to 16*/) {
   struct motord_t* pmd = motor_num_to_descr[motornum];
   assert(pmd, "bad motor in setmotor: number %d, board %d, position %d", motornum, boardnum, motorposn);
   assert(!pmd->assigned, "motor already assigned: %s", pmd->axle_name);
   motor_selects[motornum].bd_grp2 = motorboards[boardnum - 1][0];
   motor_selects[motornum].bd_grp3 = motorboards[boardnum - 1][1];
   motor_selects[motornum].motorpos = motorposn - 1;
   pmd->assigned = true;
   pmd->board_number = boardnum;
   pmd->board_position = motorposn;
   ++num_assigned; }
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

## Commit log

2024-02-05 first created
    [digit_wheel_01_v8.f3d, multiply.xlsx]
2024-02-09 Add anticipating carriage V1
2024-02-29 more details on the carriage design
2024-03-11 V2 of the anticipating carriage design and tester
2024-04-04 added photo of carriage prototype tester
2024-05-19 add prototype controller source code
2024-09-15 Add Piers Plummer's Difference Engine CAD files
    [Base_plate.SLDPRT, Bearing_30_37_4.SLDPRT, Bearing_flanged_20_27_4.SLDPRT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]
2025-02-25 Major enhancement to including modeling of all gears and how they mesh
2025-02-25 Major enhancement to model all gears and gear meshing
2025-06-29 Add gear meshing simulator
2025-06-29 Add gear meshing analyzer
2025-07-10 expanded gear mesh analysis to do all Mill loops
2025-07-26 Alternate 5-geaer mesh; add 3-gear mesh
2025-07-26 generalize mesh analysis routines for any number of gears
2025-11-02 Add prototype V2 information, etc.
2025-11-05 update prototype V2 firmware
2026-04-22 update prototype firmware and boards
2026-05-10 Create carriage v1 oblique.mp4
